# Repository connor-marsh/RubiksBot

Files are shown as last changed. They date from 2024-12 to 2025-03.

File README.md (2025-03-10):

# RubiksBot

demo  
If this embedded video isn't working, instead check out: [Demo on Youtube](https://www.youtube.com/shorts/OHwuC508IQA)

Repository for code, schematics, and designs for my Rubik's cube solving robot. This project was made as my final project for the University of Pittsburgh Swanson School of Engineering, Electrical and Computer Engineering class: Junior Design Fundamentals. All purchases made for this project were funded by the Electrical and Computer Engineering department so huge thanks to them and to Dr. Dickerson for creating and teaching this class. This is the third and final project of the class, giving me only a total of 4 weeks to make this project (We technically had 6 weeks but the first two I was too busy with other projects due earlier to start this). The extremely tight 4 week deadline for this project was the main driving factor in many of my design decisions.

### My background
###### Engineering
I have been making hobby coding and engineering projects since middle school. I am currently studying computer engineering at the University of Pittsburgh

###### Rubik's Cubes
I learned how to solve a Rubik's cube in 5th grade. I immediately got into speedcubing after that which is the sport of trying to solve cubes as fast as possible. I wasn't too good in 5th grade my best time was around 40 seconds, and I stopped practicing much by the start of 6th grade. When the COVID lockdown happened in 2020 I picked back up the hobby and improved loads. I got my best solve time down to 9 seconds with an average time of 15 seconds. I also learned how to solve the cube blindfolded and got into an event called MultiBlind, where you have one hour total to memorize as many cubes as you can, put on a blindfold, then solve them all in one go. Here's a link to me doing that on youtube: [My cubing youtube channel](https://www.youtube.com/@5mover131)

### Design basics
###### Inspiration
This robot was partially inspired by the GAN Robot's design which uses 5 total motors, with the 4 equatorial motors being able to move in and out to allow for easy insertion and removal of the cube. I wanted to design this project from scratch and not copy any existing resources, so although I know of the GAN Robot's existence, I deliberately chose to not look at it at all after starting this project. The last time I looked at the GAN Robot was a few years ago when I saw videos of it after its release.
###### Motors
The robot uses 5 Nema17x60mm Stepper motors to turn the cube sides. Each stepper is driven by a TB6600 Stepper Driver. I chose these motors and drivers to guarantee enough torque and speed since with my time constraint on this project I couldn't afford to not have strong enough motors and need to order new ones. I also chose to use Stepper motors for their ease of control/use, and their inherit accuracy. I didn't want to waste valuable time dealing with encoders/other sensors.
The 5 motors are placed similarly to the GAN robot, with one on the bottom and four around the equator. The equator motors are all slotted inside a groove and can slide back and forth to allow for easy cube insertion and removal. In the future I plan to add a mechanism to automatically slide them forward and backwards but right now that needs to be done manually.  
Full setup:  
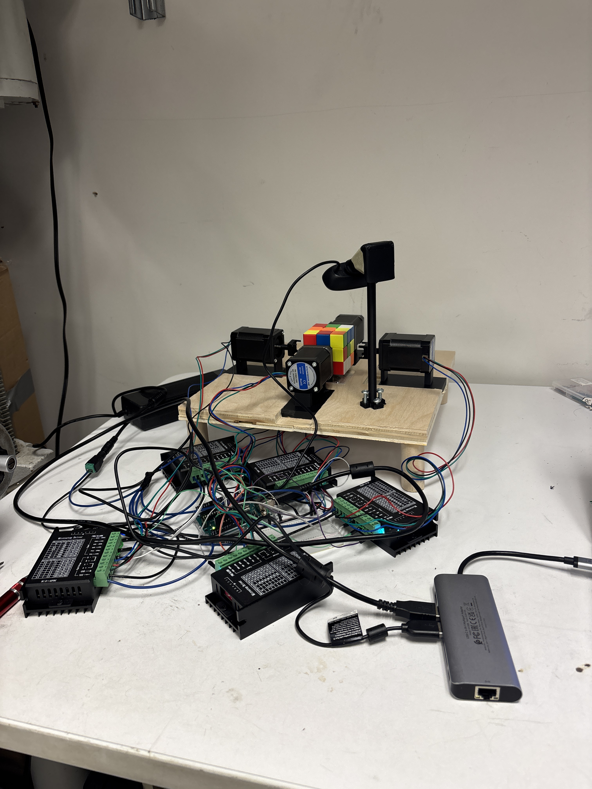
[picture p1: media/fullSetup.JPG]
Full Setup


###### Sensing
There is a camera mounted on the main board where the cube is, positioned above and diagonally away from the cube. This is done so that when the equator motors are pulled back, and the bottom motor rotates the cube to a 45 degree offset from a cardinal direction, the camera can see both the top face and one side face straigth on. Then the bottom motor can rotate 90 degrees 4 times and the camera can take a picture each time. This gets us 4 photos, which show us the top side of the cube (4 times) and each equator side (once). With the knowledge of 5 sides of the cube we can deduce the sixth side easily.  
Camera Mount:  
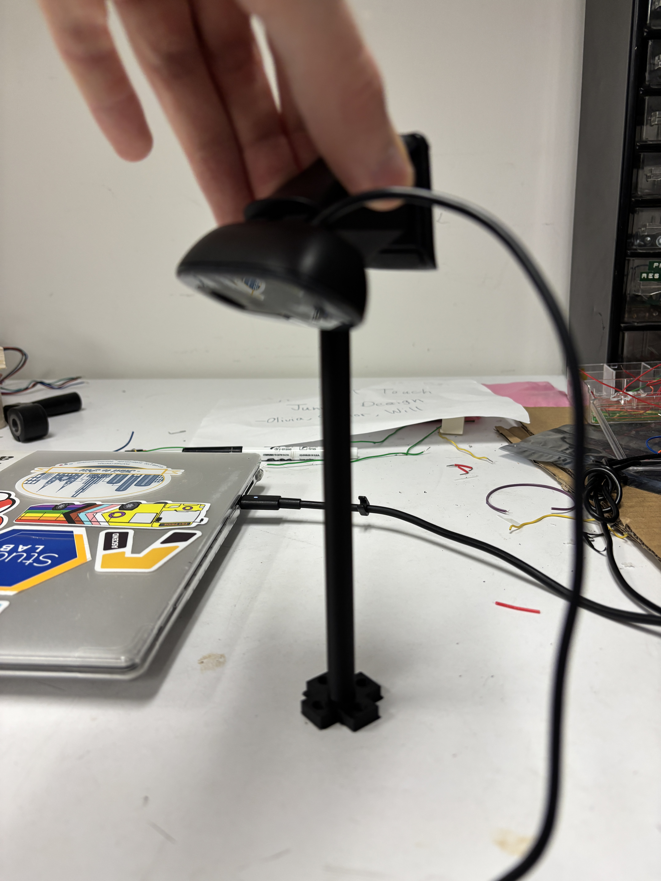
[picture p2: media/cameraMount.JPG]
Camera Mount


###### Solving
There is an existing algorithm called Kociemba's algorithm which has been mathematically proven to be the optimal algorithm for solving any possible cube state. With my time constraint I didn't want to spend time creating my own cube solving implementation so I decided to just copy the source code for Kociemba's algorithm from an open source github page I found. It does need to be a slightly modified Kociemba because we only have 5 degrees of freedom, when the normal algorithm assumes 6.

###### Control
Currently the robot is controlled by having my computer send motor angles to an Arduino via Serial, and the Arduino is running a program that just constantly reads motor angles from Serial and turning the steppers to those angles accordingly. It also does some additional processing to do thing like smoothly accelerating and deaccelerating the motors etc.

###### CAD Modeling
The robot was modeled in Fusion360 all the parts were either printed on RAS’s Bambu X1 Carbon, the Prusa in the Classroom to community room 437, or machined on the makerspace’s xcarve!  
Full robot CAD (with only one of the equator motors visible for clarity):
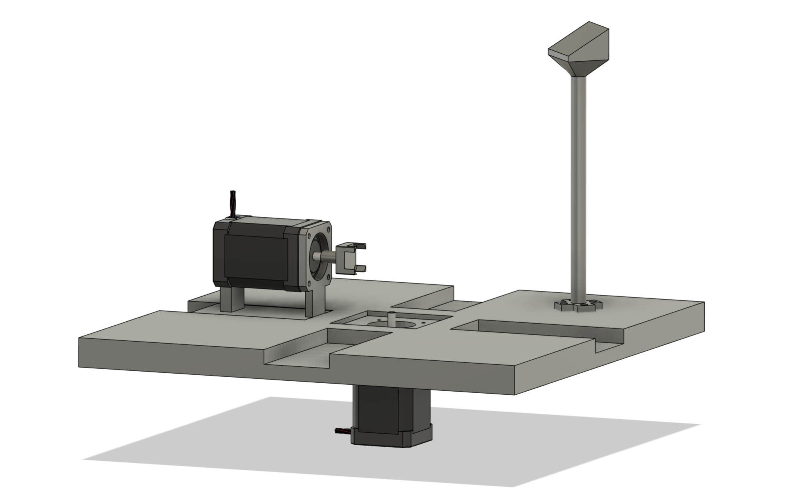
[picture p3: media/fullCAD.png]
FullCAD
  
Camera mount CAD:  
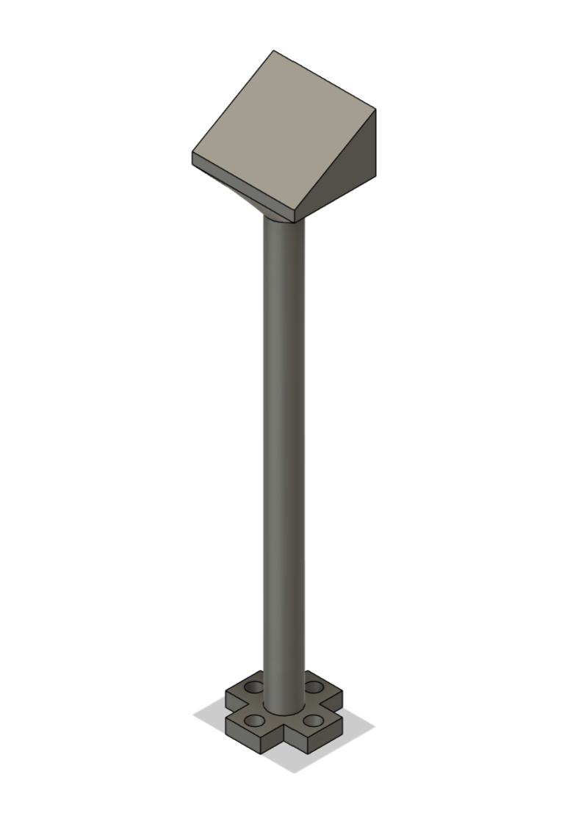
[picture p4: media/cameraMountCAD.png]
Camera CAD
  
Motor shaft adapter/cube turner CAD:  
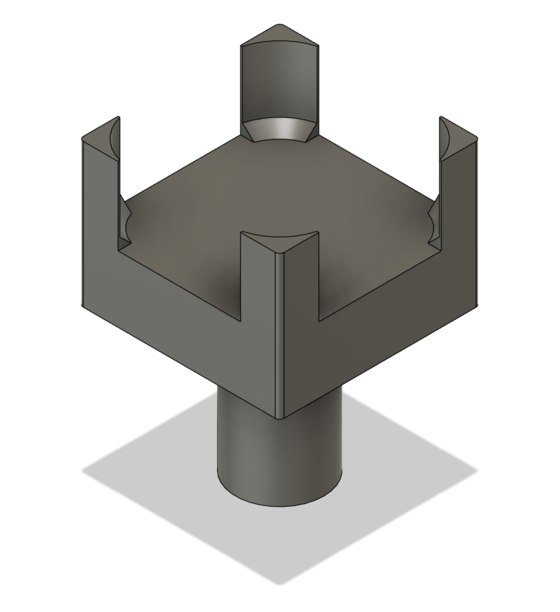
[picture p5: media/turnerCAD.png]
Turner CAD
  
Board being machine on the XCARVE:  
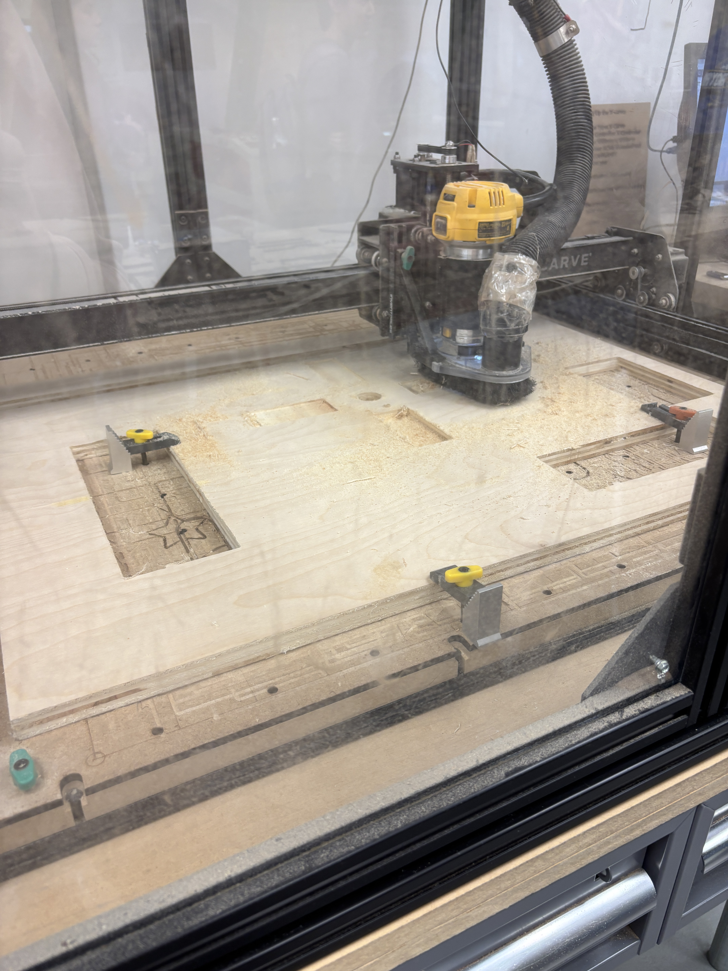
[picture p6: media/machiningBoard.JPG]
Machining


###### Preliminary Testing
Over thanksgiving break I did a lot of preliminary testing for the motor driving and control, and for the computer vision, as those were two components of the project I could work on from home and figured would be very important and time consuming.  
To test the motors I just used my Arduino plus one motor and one driver. At the time I only had 1 motor and 3 drivers because of issues with ordering parts from amazon but it was all good.
Testing the max speed I could drive the cube:  
fast turning

For CV Testing, I just used an old webcam I had on hand and started figuring out my CV program, I got most of this done over break and just needed fine tuning/improvements to be done later for increased accuracy!  
CV Test setup:  
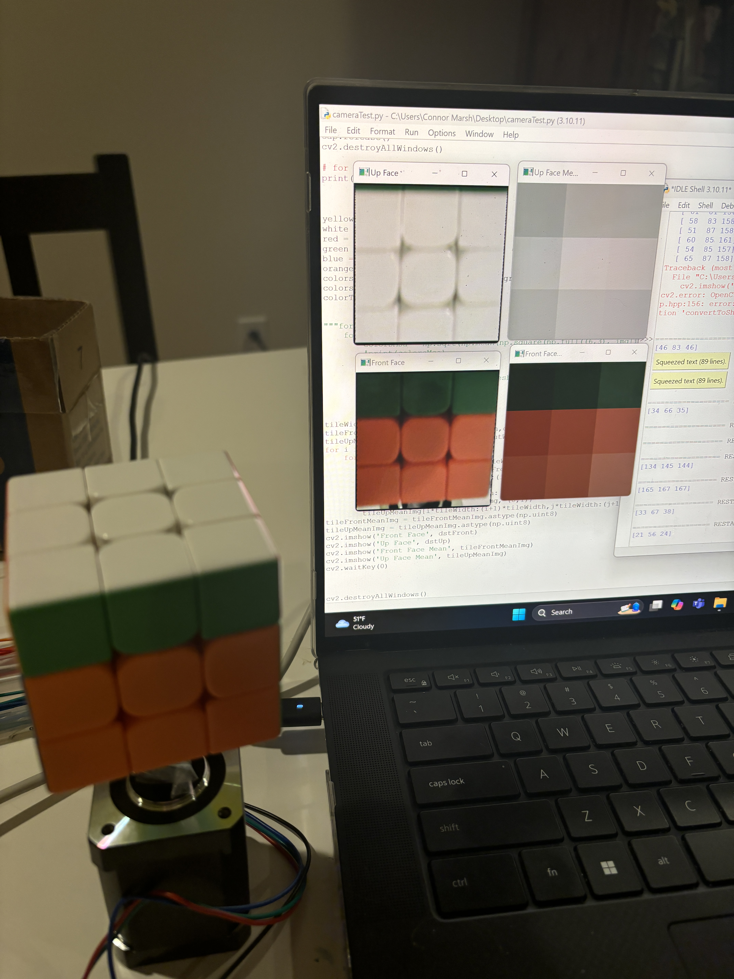
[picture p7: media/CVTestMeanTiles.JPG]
CV Mean Tiles
  
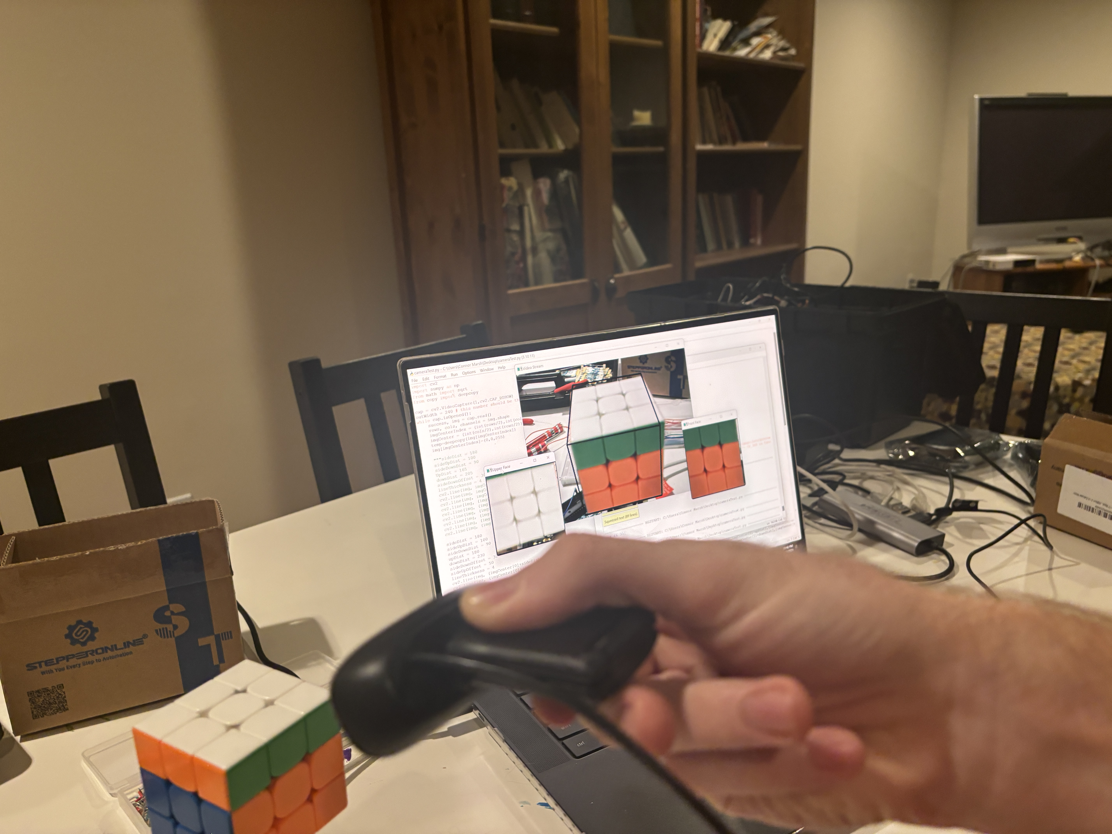
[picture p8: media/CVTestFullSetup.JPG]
CV Full setup


##### Final Design Testing
To test my design I setup the robot in the RAS shop and individually tested and confirmed functionality of all the important components: motor control, CV, and cube solving algorithm. To confirm motor control I had an Arduino program that just did hardcoded move sequences. To test CV I just took the pictures manually and made sure the cube state outputs were correct. And to test the cube solving algorithm I manually typed in the cube state, got the solution, then manually performed the solution to make sure it solved the cube.  
After I got these 3 major components working independently, I combined them all together into the main program, which included interfacing my computer with the Arduino via serial. When everything was put together it introduced some bugs as expected but they were all easily resolved.  
###### Some issues I had along the way and how I fixed them
Red and orange being very similar and hard to distinguish. I fixed this by sorting the 18 most red and orange seeming pieces by hue and taking the 9 lowest hues and calling them red and the 9 highest and calling them oranged. This fixed the problem of the actual threshold changing based on lighting and shadows.  
Cube jamming and vibrations. When I tried to run the cube at a high speed the motors would vibrate too much and cause jams. I fixed this by adding acceleration into the motor control to smooth out the starts and ends of the turns while still allowing a very high max speed!  
##### Summary and future work
In summary this was a great success! As you saw during the live demonstration the robot is working very well! It solves the cube *most* of the time apart from small mechanical issues that can be fixed later. For future work, I would improve the solving algorithm to go from 60 move solves on average to 25. And I would also add linear actuators on the equator motors to make them move in and out automatically for a fully automated system.

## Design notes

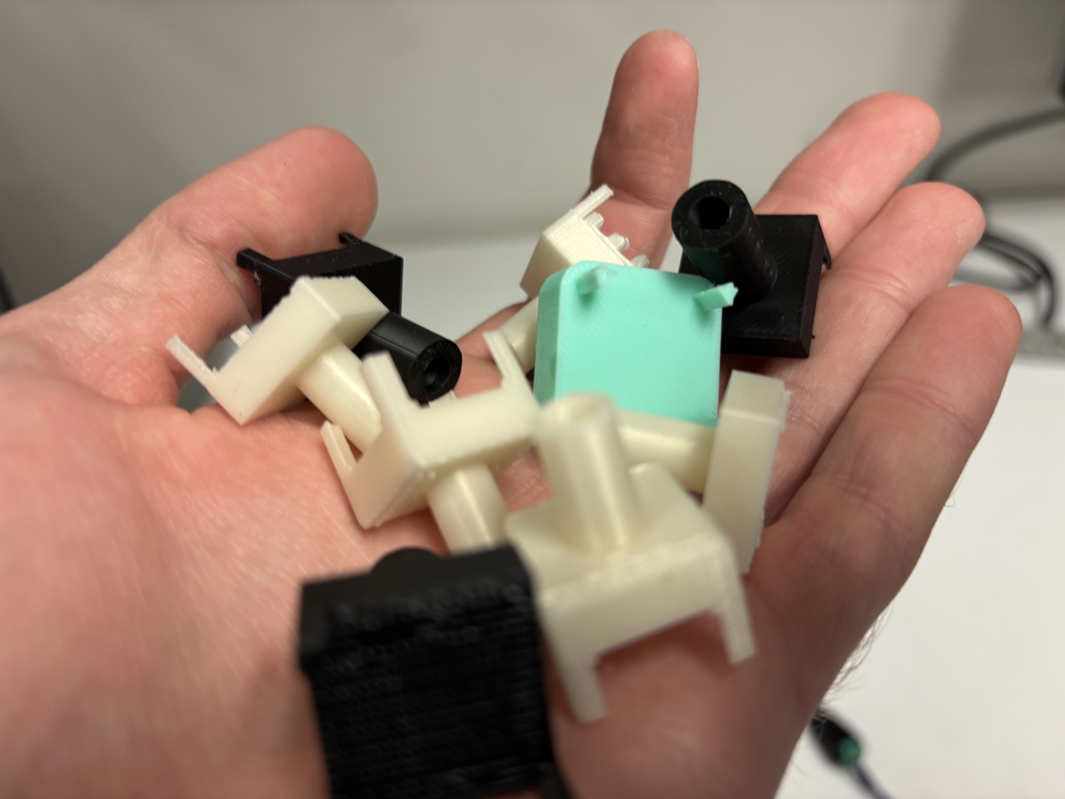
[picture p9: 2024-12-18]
media/turnerIterations.JPG

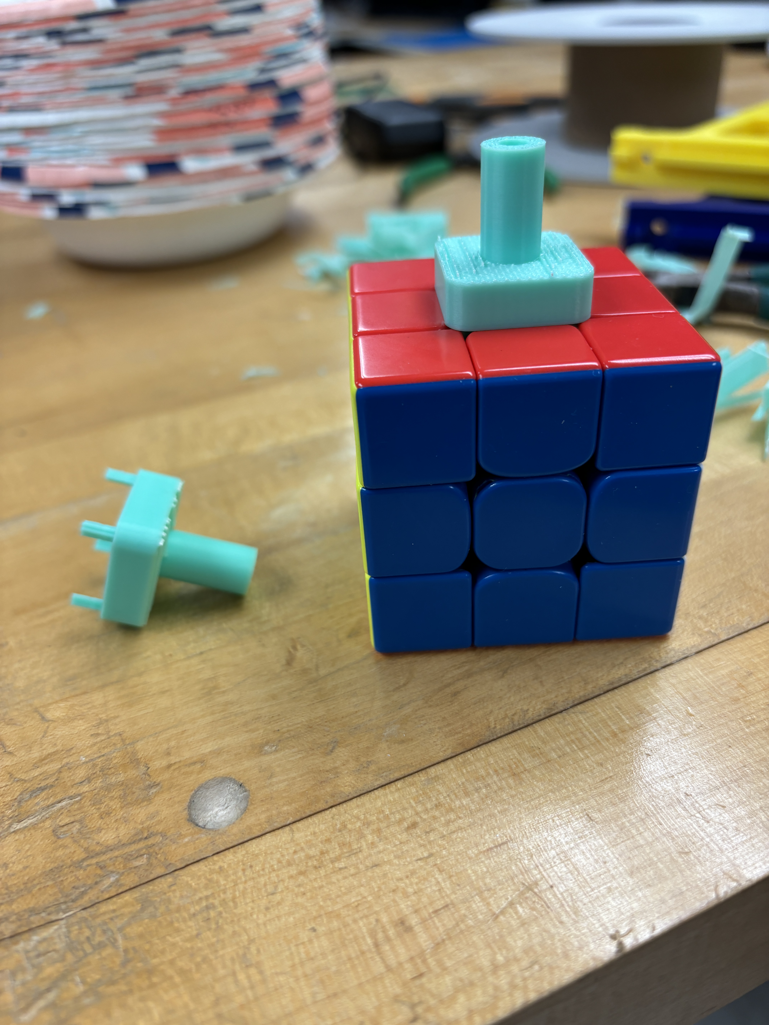
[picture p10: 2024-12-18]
media/initialTurners.JPG

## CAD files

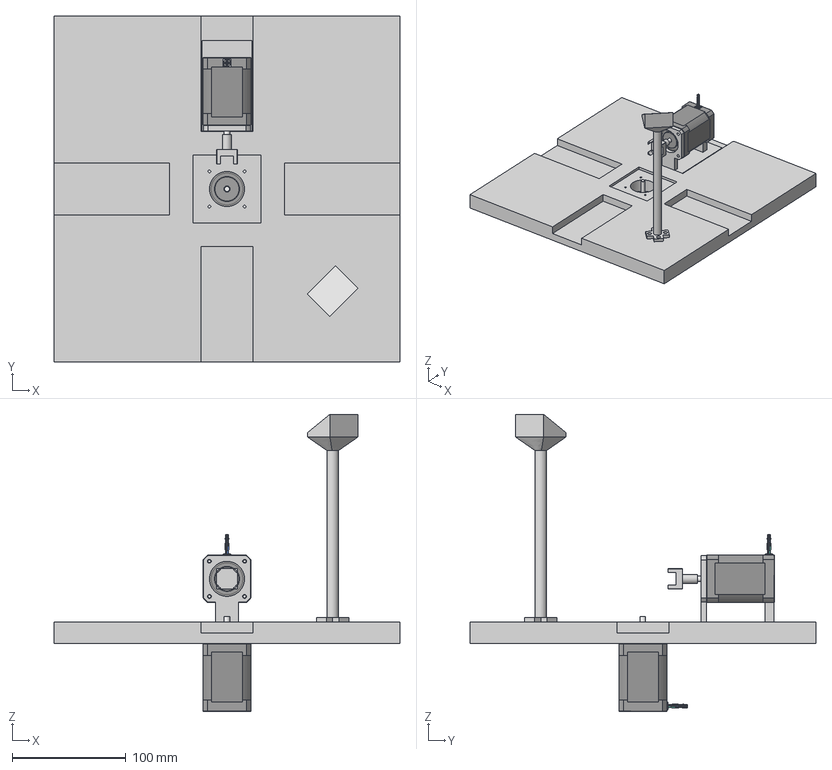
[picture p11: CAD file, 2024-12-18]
cad/Rubik'sRobot.step
304.8 x 304.8 x 262.0 mm
Copper-2of4 x 2
Frontplate x 2
Backplate x 2
Connenctor x 2
Housing x 2
Bearing dummy x 2
Bearing dummy 01 x 2
Core x 2
M3x52-Screw x 2
M3x52-Screw007 x 2
M3x52-Screw008 x 2
M3x52-Screw009 x 2
Cable-1of4 x 2
Copper-1of4 x 2
Cable-2of4 x 2
Copper-4of4 x 2
Cable-3of4 x 2
Copper-3of4 x 2
Cable-4of4 x 2
CameraMount

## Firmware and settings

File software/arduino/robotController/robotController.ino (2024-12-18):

#define NUM_MOTORS 5
#define STEP_US 40
#define STEP_US_MAX 8 // 8 is the minimum, 20 is good rn
#define STEP_US_SLOW 30
int stepUsMax = STEP_US_MAX;
#define STEP_US_START 60
#define STEP_ACCEL 4
#define WAIT_PER_TURN 0 // 10 to be safe, 30 to be extra safe, none needed
#define STEPS_PER_REV 6400 // maximum amount of microstepping for smoothest operation
#define R 0
#define F 1
#define L 2
#define B 3
#define D 4
#define C 90
#define CC -90
#define C2 180
#define C0 45
#define C1 -45
#define MAX_INPUT 400 // for reading serial

int dirPins[NUM_MOTORS] = {2, 4, 6, 8, 10};
int stepPins[NUM_MOTORS] = {3, 5, 7, 9, 11};

bool movesToDo = false;
String moveString;



void setup() {
  Serial.begin(115200);
  // put your setup code here, to run once:
//  pinMode(DIR_PIN, OUTPUT);
//  pinMode(STEP_PIN, OUTPUT);
  for (int i = 0; i < NUM_MOTORS; i++) {
    pinMode(dirPins[i], OUTPUT);
    pinMode(stepPins[i], OUTPUT);
  }
  delay(5000); // delay to plug in power
}

void loop() {
  
  // if serial data available, process it
  while (Serial.available() > 0)
    processIncomingByte (Serial.read());

  if (movesToDo) {
    moveSequence(moveString);
    movesToDo = false;
  }

  delay(5);

}

void turnMotor(int num, int angle) {
  digitalWrite(dirPins[num], angle > 0 ? LOW : HIGH);
  int stepDelay = STEP_US_START;
  int stepsToMax = (STEP_US_START - stepUsMax)*STEP_ACCEL;
  double stepMax = STEPS_PER_REV*((double) abs(angle)/360.0);
  for (int i = 0; i < stepMax; i++) {
    digitalWrite(stepPins[num], HIGH);
    delayMicroseconds(stepDelay);
    digitalWrite(stepPins[num], LOW);
    delayMicroseconds(stepDelay);
    if (i % STEP_ACCEL == 0 and i < stepsToMax) {
      stepDelay--;
    }
    else if (i % STEP_ACCEL == 0 and i > stepMax-stepsToMax) {
      stepDelay++;
    }
    //Serial.println(stepDelay);
  }
  if (WAIT_PER_TURN>0)
    delay(WAIT_PER_TURN);
}

void turn2Motors(int num1, int angle1, int num2, int angle2) {
  digitalWrite(dirPins[num1], angle1 > 0 ? LOW : HIGH);
  digitalWrite(dirPins[num2], angle2 > 0 ? LOW : HIGH);
  double max1 = STEPS_PER_REV*((double) abs(angle1)/360.0);
  double max2 = STEPS_PER_REV*((double) abs(angle2)/360.0);
  double overallMax = max(max1, max2);
  for (int i = 0; i < overallMax; i++) {
    if (i < max1)
      digitalWrite(stepPins[num1], HIGH);
    if (i < max2)
      digitalWrite(stepPins[num2], HIGH);
    delayMicroseconds(STEP_US);
    if (i < max1)
      digitalWrite(stepPins[num1], LOW);
    if (i < max2)
      digitalWrite(stepPins[num2], LOW);
    delayMicroseconds(STEP_US);
  }
  // when different length moves delay extra long to stop jams
  if (max1 == max2)
    delay(WAIT_PER_TURN);
  else
    delay(WAIT_PER_TURN*2);
}

void moveSequence(String moveString) {
  int numMoves = 0;
  // Move sequence will never be longer than half the max allowed serial input
  // since that input has spaces between every letter
  int moves[MAX_INPUT/2];
  int angles[MAX_INPUT/2];
  for (int i = 0; i < moveString.length(); i++) {
    if (moveString[i] == 'R' || moveString[i] == 'F' || moveString[i] == 'D' || moveString[i] == 'L' || moveString[i] == 'B') {
      // get type/direction of move
      if (i < moveString.length()-1) { // to prevent out of bounds
        if (moveString[i+1] == '\'') { // counterclockwise
          angles[numMoves] = CC;
        }
        else if (moveString[i+1] == '2') { // half-turn
          angles[numMoves] = C2;
        }
        else if (moveString[i+1] == '0') { // clockwise eighth turn
          angles[numMoves] = C0;
        }
        else if (moveString[i+1] == '1') { // cc eighth turn
          angles[numMoves] = C1;
        }
        else { // clockwise
          angles[numMoves] = C;
        }
      }
      else {
        angles[numMoves] = C;
      }

      // get cube side
      switch (moveString[i]) {
        case 'R':
          moves[numMoves] = R;
          break;
        case 'F':
          moves[numMoves] = F;
          break;
        case 'D':
          moves[numMoves] = D;
          break;
        case 'L':
          moves[numMoves] = L;
          break;
        case 'B':
          moves[numMoves] = B;
          break;
      }
      numMoves++;
    }
  }
  //Serial.println(numMoves);
  if (numMoves < 5) {
    stepUsMax = STEP_US_SLOW;
  }
  else {
    stepUsMax = STEP_US_MAX;
  }
  // now we have our moves broken down into a form that can be handled by the overloaded moveSequence function
  moveSequence(moves, angles, numMoves);
  Serial.println("Move sequence completed");
}

void moveSequence(int* moves, int* angles, int numMoves) {
  bool did2Motors = false;
  for (int i =0; i < numMoves; i++) {
    // uncomment this to do 2 motors at once
    // skip current instruction if last instruction we did 2 at once
//    if (did2Motors) {
//      did2Motors = false;
//      continue;
//    }
//    // see if we can do 2 turns at once
//    if (i < numMoves-1) {
//      if (abs(moves[i]-moves[i+1]) == 2) {
//        //execute 2 turns at once
//        turn2Motors(moves[i], angles[i], moves[i+1], angles[i+1]);
//        did2Motors = true;
//      }
//    }
    if (!did2Motors) {
      turnMotor(moves[i], angles[i]);
    }
  }
}



// here to process incoming serial data after a terminator received
void process_data (const char * data, int dataLen)
{
  moveString = String(data);
  if (dataLen > 0) {
    movesToDo = true;
  }
    
}  // end of process_data

void processIncomingByte (const byte inByte)
{
  static char input_line [MAX_INPUT];
  static unsigned int input_pos = 0;

  switch (inByte)
  {

    case '\n':   // end of text
      input_line [input_pos] = 0;  // terminating null byte

      // terminator reached! process input_line here ...
      process_data (input_line, input_pos);

      // reset buffer for next time
      input_pos = 0;  
      break;

    case '\r':   // discard carriage return
      break;

    default:
      // keep adding if not full ... allow for terminating null byte
      if (input_pos < (MAX_INPUT - 1))
        input_line [input_pos++] = inByte;
      break;

  }  // end of switch

} // end of processIncomingByte

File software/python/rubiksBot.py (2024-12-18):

import kociemba
import serial.tools.list_ports
from time import sleep
import cv2
import numpy as np
from math import sqrt
from copy import deepcopy
import os

# Serial setup stuff
ports = serial.tools.list_ports.comports()
serialInst = serial.Serial()
portsList = []

for one in ports:
    portsList.append(str(one))
    print(str(one))

serialInst.baudrate = 115200
serialInst.port = "COM9"
serialInst.open()



print("Sleeping to allow time for Serial to connect")
sleep(8)
print("Done sleeping")

def runMoves(moves):
    serialInst.write((moves+"\n").encode('utf-8'))
    serialInst.readline() #wait for completion

# some solve string manipulation stuff
def removeU(moves):
    output = ""
    prevU = False
    counter = 0
    for move in moves:
        counter+=1
        if move == "U":
            if counter == len(moves):
                output += "R L F2 B2 R' L' D R L F2 B2 R' L'"
            else:
                prevU = True
                continue
        elif prevU:
            prevU = False
            if move == " ":
                output += "R L F2 B2 R' L' D R L F2 B2 R' L' "
            elif move == "'":
                output += "R L F2 B2 R' L' D' R L F2 B2 R' L'"
            else:
                # half turn
                output += "R L F2 B2 R' L' D2 R L F2 B2 R' L'"
        else:
            output += move
    return output
def collapseRedundantMoves(moves):
    moveList = moves.split(" ")
    output = recurseCollapse(moveList)
    return " ".join(output)
oppositeMoves = {
    "R":"L",
    "L":"R",
    "F":"B",
    "B":"F",
    "U":"D",
    "D":"U"
}
def recurseCollapse(moveList):
    newList = []
    collapsed = False
    i = 0
    while i < len(moveList): # doing C style for loop to allow for skipping multiple iterations easier
        if i < len(moveList)-1 and moveList[i][0] == moveList[i+1][0]: # if two consecutive moves turn the same side
            collapsed = True # We can collapse
            if len(moveList[i])==1:
                angle1 = 90
            elif moveList[i][1]=='2':
                angle1 = 180
            else:
                angle1 = -90
            if len(moveList[i+1])==1:
                angle2 = 90
            elif moveList[i+1][1]=='2':
                angle2 = 180
            else:
                angle2 = -90
            if angle1+angle2 == 90: #normal clockwise move
                newList.append(moveList[i][0])
            elif angle1+angle2 == 180: # half turn
                newList.append(moveList[i][0]+'2')
            elif (angle1+angle2)%360 == 270: # counterclockwise
                newList.append(moveList[i][0]+"'")
            # note that if angle1+angle2 == 0 then we do nothing and those 2 moves disappear
            i += 1 # increment i to skip over the next 1 items
        # check if two moves that turn the same side sandwich a move that turns the opposite side
        
        elif i < len(moveList)-2 and moveList[i][0] == moveList[i+2][0] and moveList[i][0] == oppositeMoves[moveList[i+1][0]]:
            collapsed = True # We can collapse
            if len(moveList[i])==1:
                angle1 = 90
            elif moveList[i][1]=='2':
                angle1 = 180
            else:
                angle1 = -90
            if len(moveList[i+2])==1:
                angle2 = 90
            elif moveList[i+2][1]=='2':
                angle2 = 180
            else:
                angle2 = -90
            if (angle1+angle2)%360 == 90: #normal clockwise move
                newList.append(moveList[i][0])
            elif (angle1+angle2)%360 == 180: # half turn
                newList.append(moveList[i][0]+'2')
            elif (angle1+angle2)%360 == 270: # counterclockwise
                newList.append(moveList[i][0]+"'")
            # note that if angle1+angle2 == 0 then we do nothing and those 2 moves disappear
            newList.append(moveList[i+1]) # make sure to add the sandwiched moves
            i += 2 # increment i to skip over the next 2 items
        else:
            newList.append(moveList[i])
        i += 1
    if collapsed:
        return recurseCollapse(newList)
    else:
        return moveList # if no collapse then moveList=newList

# CV setup stuff
cap = cv2.VideoCapture(1,cv2.CAP_DSHOW)
outWidth = 240 # this number should be threeven for simplicity sake

#pts for cube borders
# also pls dont judge me for making these two separate variables it was just faster to use
# with open cv calls. I know its a bad method

pts1 = []
pts2 = []
pts3 = []
if os.path.exists('cubePts1.txt'):
    with open('cubePts1.txt', 'r') as file:
        for line in file:
            # Convert each line to a list of integers and append it to read_list
            pts1.append(list(map(int, line.split())))
else:
    pts1 = [[530, 260],[148, 260],[480, 33],[188, 33]] # default pts1

if os.path.exists('cubePts2.txt'):
    with open('cubePts2.txt', 'r') as file:
        for line in file:
            # Convert each line to a list of integers and append it to read_list
            pts2.append(list(map(int, line.split())))
else:
    pts2 = [[530, 270],[148, 270],[475, 460],[186, 450]] # default pts2

if os.path.exists('cubePts3.txt'):
    with open('cubePts3.txt', 'r') as file:
        for line in file:
            # Convert each line to a list of integers and append it to read_list
            pts3.append(list(map(int, line.split())))
else:
    pts3 = [[283, 279],[59, 120],[493, 118],[279, 0]] # default pts3
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
